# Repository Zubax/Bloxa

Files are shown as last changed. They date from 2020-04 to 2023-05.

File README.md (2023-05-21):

# Zubax Bloxa

Zubax Bloxa is arguably the most compact practical ESC reference design based on [**Mitochondrik LV**](https://zubax.com/mitochondrik-lv). The key design requirements for Bloxa are:

* compactness;
* low mass;
* low COG;
* compatibility with the [UCANPHY standard](https://forum.opencyphal.org/t/cyphal-can-physical-layer-specification-v1-0/1471).

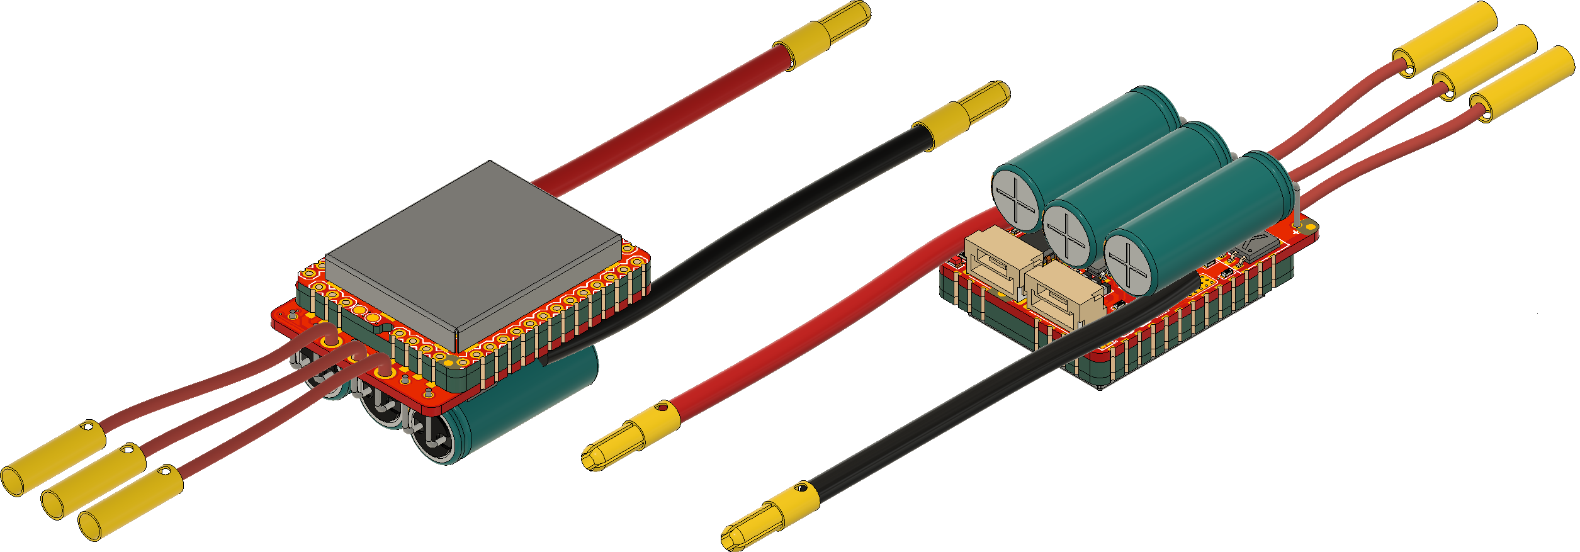
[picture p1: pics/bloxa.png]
Bloxa top


## Brief specs

* Operating voltage range: **4–8S** Li-ion (LiCoO<sub>2</sub>), 12–34 V
* Continuous power: **200 W**
* Single **Cyphal/CAN** interface
* Software-controllable **5V BEC** output connected to the CAN 5V line
* Aux port available on PCB pads (requires soldering); this port can be used for **RC PWM input** or for connecting the **motor temperature sensor**.
* Dimensions: 36.6x24.9 mm

The main advantage of Bloxa is its miniature size. To achieve it, a novel Mitochondrik mounting technique is used.

<p align="center">
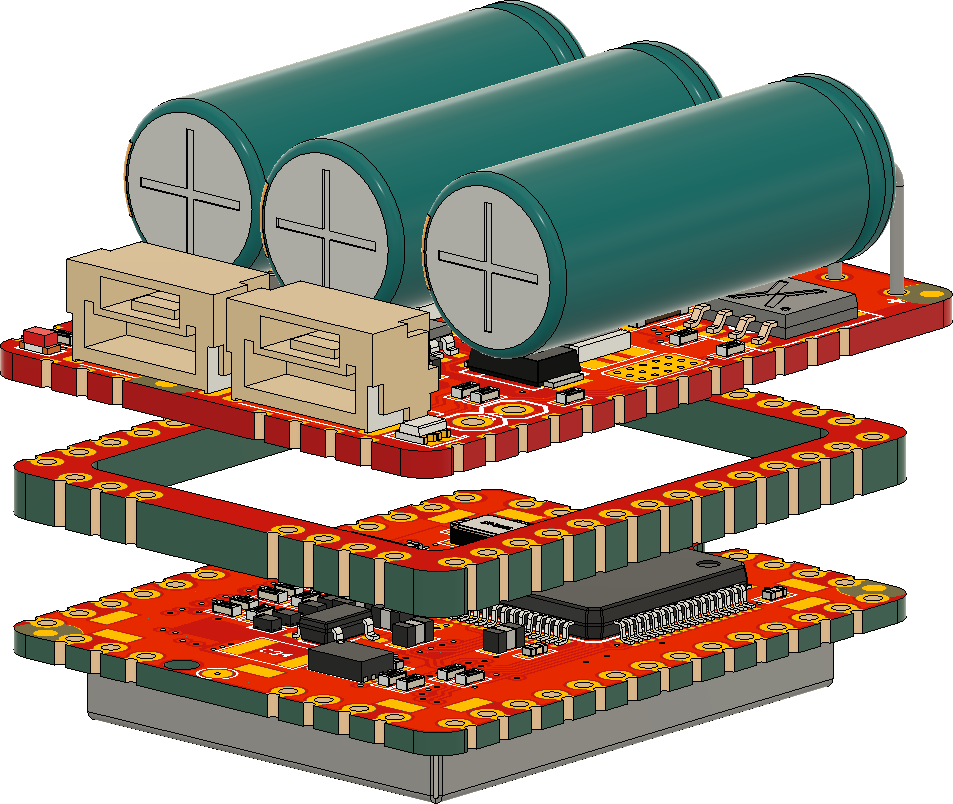
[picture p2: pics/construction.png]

</p>

Mitochondrik is mounted on the power stage PCB using an intermediary 2 mm thick PCB that serves as a connector.
Soldering is done using the edge connectors on the Mitochondrik, the intermediary  PCB, and the power stage PCB in the plane perpendicular to the PCB planes. 
Also, one of the RF shields on the Mitochondrik needs not be installed (Mitochondrik modules without the RF shield are available upon request, please contact Zubax Robotics).

<p align="center">
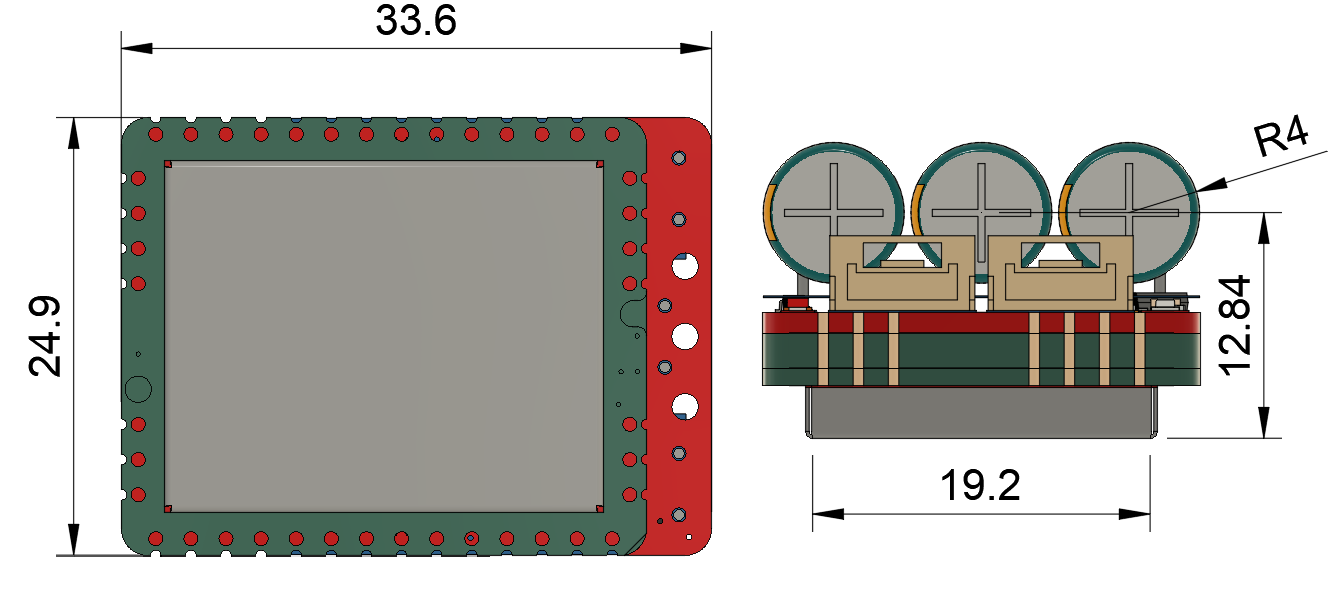
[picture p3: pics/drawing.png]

</p>

## Power stage details.

Bloxa power stage uses three BUK9K6R2-40E MOSFET arrays.

| Parameter | Value |
| :--- | --- |
| Drain to Source Voltage (V<sub>ds</sub>) | 40 V |
| Current - Continuous Drain (I<sub>d</sub>) @ 25°C | 40 A |
| R<sub>ds on</sub> (Max) @ I<sub>d</sub>, V<sub>gs</sub> | 6 mOhm @ 25 A, 10 V |
| Gate Charge (Q<sub>g</sub>) (Max) @ V<sub>gs</sub> | 35.4 nC @ 10 V |

The bulk capacitor bank is formed with 3 [180 µF aluminum electrolytic capacitors](https://www.digikey.com/products/en?keywords=565-4066-ND) from [United Chemi-Con](https://www.digikey.com/en/supplier-centers/u/united-chemi-con).

## Release notes

Newest entries at the top.

### Bloxa v1.0

* Hardware over-current protection resistor has been adjusted in accordance with the latest design recommendations. See the [Mitochondrik LV](https://zubax.com/mitochondrik-lv) datasheet for details.
* Current shunts replaced with 3 mohms.

### Bloxa v0.2

* Current shunts replaced (5 mohms replaced with 10 mohms).
* Overcurrent protection added. Itrip is ~35 A.
* RCPWM through-hole connector replaced with smd solder pads.
* Power loss estimations table added to the schematic.
* TVS diode (D1) replaced with one that has lower breakdown voltage.

## License

This project is licensed under the terms of [CC-BY 4.0](https://creativecommons.org/licenses/by/4.0/).

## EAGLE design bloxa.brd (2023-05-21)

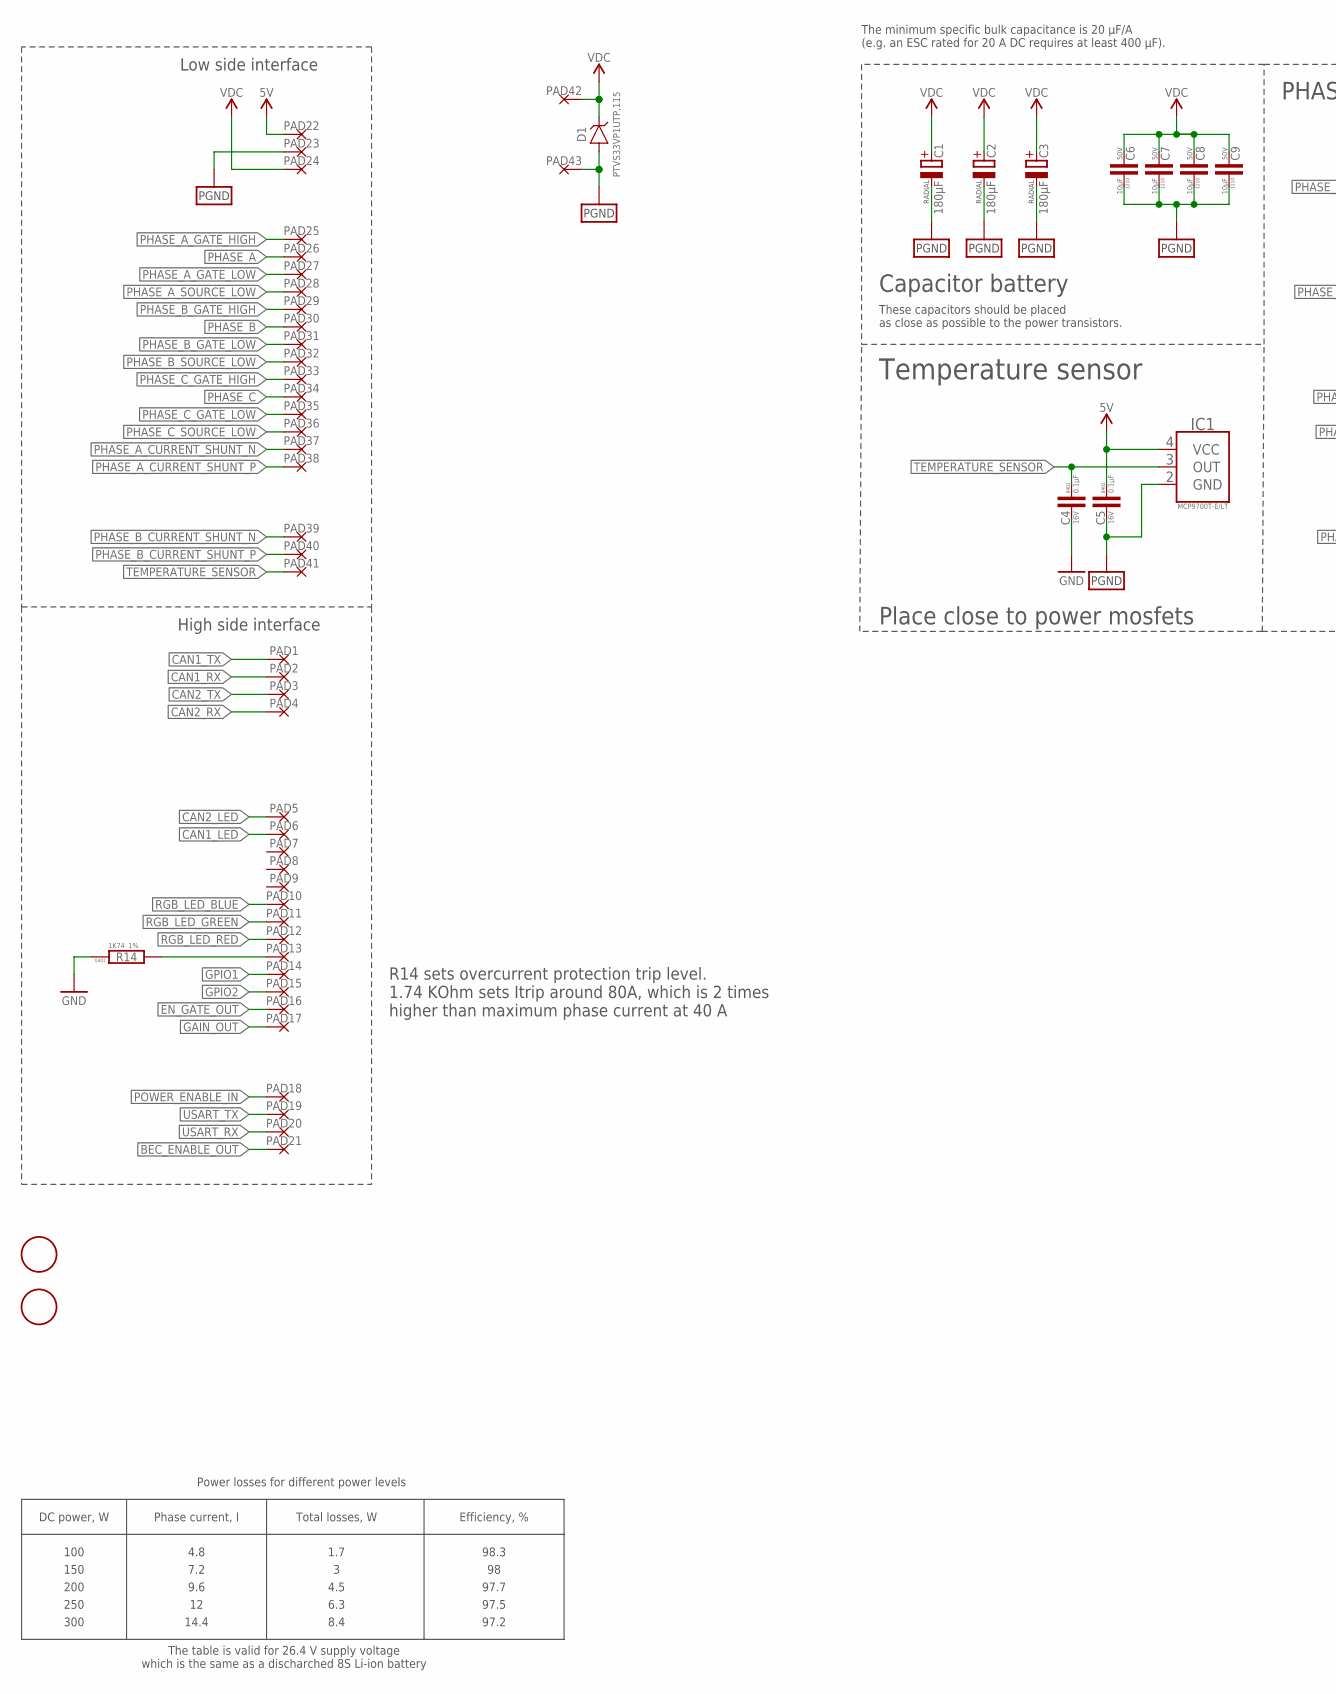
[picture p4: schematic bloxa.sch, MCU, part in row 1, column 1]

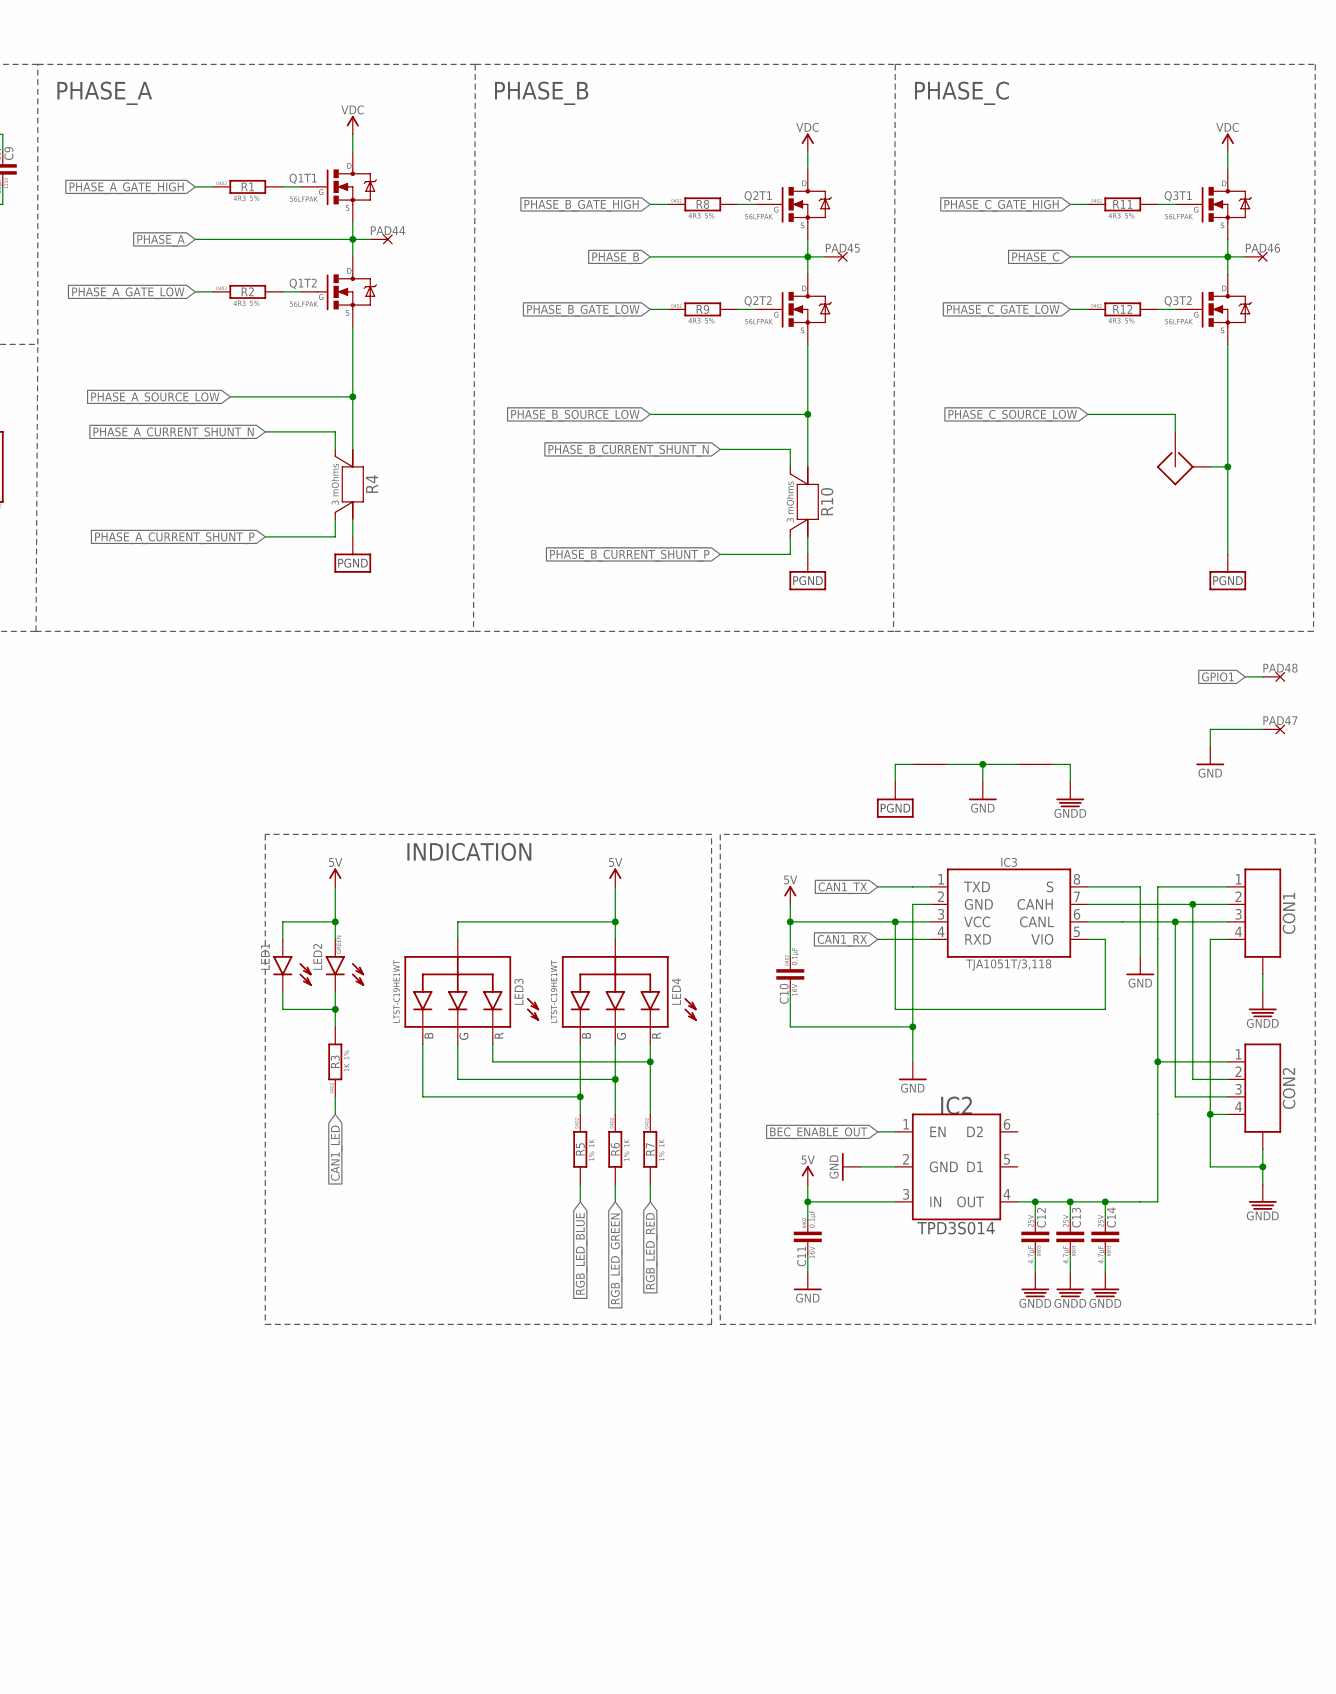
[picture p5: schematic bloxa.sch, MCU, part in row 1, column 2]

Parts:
C1, C2, C3: 180µF; RADIAL_SIDE_8X21.5
C4, C5, C10, C11: 0.1µF; C0402
C6, C7, C8, C9: 10µF; C1210
C12, C13, C14: 4.7µF; C0603
CON1, CON2: CON-4P-JST_GH-RA; JST_GH-4P-RA
D1: PTVS33VP1UTP,115-36V-SOD128; SOD128
FD1, FD2: FIDUCIALMOUNT; FIDUCIA-MOUNT
IC1: MCP9700-SC70-5; SC70-5
IC2: TPD3S014DBVR-SOT23-6; SOT26
IC3: TJA1051(X)/3-SO8; SOIC8
J1, J2: CONNECTION
LED1: GREEN; LED0402
LED2: GREEN; LED0402; DIGIKEY# 1830-IN-S42BT5GCT-ND
LED3, LED4: LTST-C19HE1WT; 0606
PAD1, PAD2, PAD3, PAD4, PAD22, PAD23, PAD24: PAD-1X1.5; SMD_1X1,5
PAD5, PAD6, PAD7, PAD8, PAD9, PAD10, PAD11, PAD12, PAD13, PAD14, PAD15, PAD16, PAD17, PAD18, PAD19, PAD20, PAD21, PAD25, PAD26, PAD27, PAD28, PAD29, PAD30, PAD31, PAD32, PAD33, PAD34, PAD35, PAD36, PAD37, PAD38, PAD39, PAD40, PAD41: PAD-HOLE-0.6; HOLE_0.6
PAD42, PAD43: PAD-4X2; 4X2
PAD44, PAD45, PAD46: PAD-HOLE_1.5; HOLE_1.5
PAD47, PAD48: PAD-S-1.5; 1.5X1.5
Q1, Q2, Q3: BUK9K6R2-40E,115; SOT-1205
R1, R2, R8, R9, R11, R12: 4R3; R0402
R3, R5, R6, R7: 1K; R0402
R4, R10: 3 mOhms; R2512-KELVIN; DIGIKEY# 2019-TLR3APSDTE3L00F50CT-ND
R14: 1K74; R0402; DIGIKEY# 541-1.74KLCT-ND
S1: SENSE; SENSE-0.6

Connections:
BEC_ENABLE_OUT: IC2.1 (EN), PAD21.P$1
CAN1_LED: PAD6.P$1, R3.1
CAN1_RX: IC3.4 (RXD), PAD2.P$1
CAN1_TX: IC3.1 (TXD), PAD1.P$1
CAN1_VDD: C12.P$2 (2), C13.P$2 (2), C14.P$2 (2), CON1.1, CON2.1, IC2.4 (OUT)
CAN2_LED: PAD5.P$1
CAN2_RX: PAD4.P$1
CAN2_TX: PAD3.P$1
EN_GATE_OUT: PAD16.P$1
GAIN_OUT: PAD17.P$1
GND: C4.2, C10.2, C11.2, IC2.2 (GND), IC3.2 (GND), IC3.8 (S), J1.P$1, J2.P$1, PAD47.P$1, R14.1
GNDD: C12.P$1 (1), C13.P$1 (1), C14.P$1 (1), CON1.4, CON1.M$0 (GND), CON1.M$1 (GND), CON2.4, CON2.M$0 (GND), CON2.M$1 (GND), J2.P$2
GPIO1: PAD14.P$1, PAD48.P$1
GPIO2: PAD15.P$1
unnamed: LED3.G, LED4.G, R6.1
unnamed: LED1.C, LED2.C, R3.2
unnamed: CON1.2, CON2.2, IC3.7 (CANH)
unnamed: CON1.3, CON2.3, IC3.6 (CANL)
unnamed: Q1.2 (G), R1.2
unnamed: Q1.4 (G), R2.2
unnamed: Q3.2 (G), R11.2
unnamed: Q3.4 (G), R12.2
unnamed: Q2.2 (G), R8.2
unnamed: Q2.4 (G), R9.2
unnamed: LED3.R, LED4.R, R7.1
unnamed: LED3.B, LED4.B, R5.1
OVERCURRENT_PROTECT_ADJ: PAD13.P$1, R14.2
PGND: C1.-, C2.-, C3.-, C5.2, C6.1, C7.1, C8.1, C9.1, D1.A, IC1.2 (GND), J1.P$2, PAD23.P$1, PAD43.P$1, Q3.3 (S), R4.2, R4.22 (2), R10.2, R10.22 (2), S1.SHELL (SHELLL)
PHASE_A: PAD26.P$1, PAD44.P$1, Q1.1 (S), Q1.5 (D), Q1.6 (D), Q1.EP-5-6 (D)
PHASE_A_CURRENT_SHUNT_N: PAD37.P$1, R4.S1
PHASE_A_CURRENT_SHUNT_P: PAD38.P$1, R4.S2
PHASE_A_GATE_HIGH: PAD25.P$1, R1.1
PHASE_A_GATE_LOW: PAD27.P$1, R2.1
PHASE_A_SOURCE_LOW: PAD28.P$1, Q1.3 (S), R4.1, R4.11 (1)
PHASE_B: PAD30.P$1, PAD45.P$1, Q2.1 (S), Q2.5 (D), Q2.6 (D), Q2.EP-5-6 (D)
PHASE_B_CURRENT_SHUNT_N: PAD39.P$1, R10.S1
PHASE_B_CURRENT_SHUNT_P: PAD40.P$1, R10.S2
PHASE_B_GATE_HIGH: PAD29.P$1, R8.1
PHASE_B_GATE_LOW: PAD31.P$1, R9.1
PHASE_B_SOURCE_LOW: PAD32.P$1, Q2.3 (S), R10.1, R10.11 (1)
PHASE_C: PAD34.P$1, PAD46.P$1, Q3.1 (S), Q3.5 (D), Q3.6 (D), Q3.EP-5-6 (D)
PHASE_C_GATE_HIGH: PAD33.P$1, R11.1
PHASE_C_GATE_LOW: PAD35.P$1, R12.1
PHASE_C_SOURCE_LOW: PAD36.P$1, S1.IN
POWER_ENABLE_IN: PAD18.P$1
RGB_LED_BLUE: PAD10.P$1, R5.2
RGB_LED_GREEN: PAD11.P$1, R6.2
RGB_LED_RED: PAD12.P$1, R7.2
TEMPERATURE_SENSOR: C4.1, IC1.3 (OUT), PAD41.P$1
USART_RX: PAD20.P$1
USART_TX: PAD19.P$1
VDC: C1.+, C2.+, C3.+, C6.2, C7.2, C8.2, C9.2, D1.C, PAD24.P$1, PAD42.P$1, Q1.7 (D), Q1.8 (D), Q1.EP-7-8 (D), Q2.7 (D), Q2.8 (D), Q2.EP-7-8 (D), Q3.7 (D), Q3.8 (D), Q3.EP-7-8 (D)
VDD_5V: C5.1, C10.1, C11.1, IC1.4 (VCC), IC2.3 (IN), IC3.3 (VCC), IC3.5 (VIO), LED1.A, LED2.A, LED3.+ (A), LED4.+ (A), PAD22.P$1

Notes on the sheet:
Low side interface
High side interface
INDICATION
The minimum specific bulk capacitance is 20 μF/A (e.g. an ESC rated for 20 A DC requires at least 400 μF).
PHASE_A
PHASE_B
PHASE_C
Capacitor battery
These capacitors should be placed as close as possible to the power transistors.
Temperature sensor
Place close to power mosfets
DC power, W
Phase current, I
Total losses, W
Efficiency, %
100
150
200
250
300
The table is valid for 26.4 V supply voltage which is the same as a discharched 8S Li-ion battery
4.8
1.7
98.3
7.2
9.6
4.5
97.7
6.3
97.5
14.4
8.4
97.2
Power losses for different power levels
R14 sets overcurrent protection trip level. 1.74 KOhm sets Itrip around 80A, which is 2 times higher than maximum phase current at 40 A

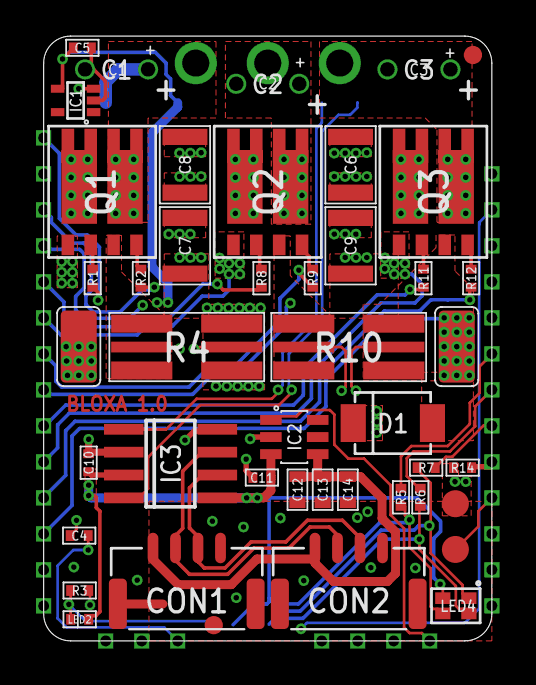
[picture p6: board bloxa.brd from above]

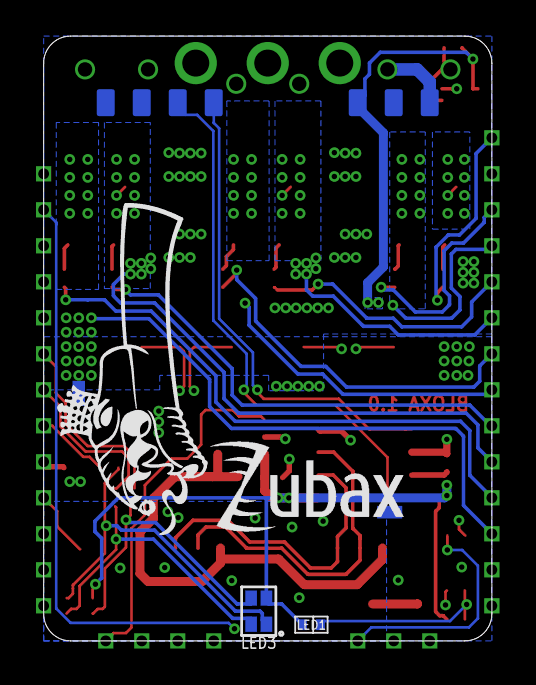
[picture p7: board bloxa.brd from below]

Board: 4 copper layers, 24.9 x 33.6 mm, 95 parts (48 on the bottom side), 44 nets.

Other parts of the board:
U$2: DRAGON-18X7
U$13: ZUBAX_LOGO_5X10

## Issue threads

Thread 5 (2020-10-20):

Update the documentation

pavel-kirienko, 2020-10-20:
- indicate that the device is based on Mitochondrik-LV
- replace the reference to UAVCAN hardware design recommendations with Cyphal/CANPHY
- bump the version number to v1.0

Afterward, tag the first v1.0 release.

Closed 2023-05-14.

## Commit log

2018-12-02 initial import
    [bloxa.brd, bloxa.sch]
2018-12-05 proper DRC and some polygons
    [bloxa.brd, bloxa.sch]
2018-12-06 more polygones
    [bloxa.brd]
2018-12-06 some progress
    [bloxa.brd, bloxa.sch]
2018-12-06 some more progress
    [bloxa.brd, bloxa.sch]
2018-12-10 more polygones updates
    [bloxa.brd]
2018-12-10 all components moved to top side
    [bloxa.brd, bloxa.sch]
2018-12-10 routing complete
    [bloxa.brd, bloxa.sch]
2018-12-12 alternate footprints for LED fancy placement
    Will never use it probably
    [bloxa.brd, bloxa.sch]
2018-12-13 assembly drawing
    [bloxa.brd]
2018-12-13 gerber files added
    [bloxa.brd, bloxa.sch]
2018-12-17 Added BOM
2019-01-26 OC_ADJ resistor added
    [bloxa.brd, bloxa.sch]
2020-09-02 Hardware files updated
    [bloxa.brd, bloxa.sch]
2020-09-02 CAM file for single PCB updated
2020-09-02 Update bloxa.sch
    Typo
    [bloxa.sch]
2023-05-14 change protection resistance
    [bloxa.brd, bloxa.sch]
2023-05-20 change Rshunt into 3mOhm
    [bloxa.brd, bloxa.sch]
2023-05-21 Remove obsolete changelog and fix the version number on the PCB
    [bloxa.brd, bloxa.sch]
